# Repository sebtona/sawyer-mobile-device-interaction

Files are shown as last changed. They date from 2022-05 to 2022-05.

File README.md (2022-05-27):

# Sawyer Mobile Device Interaction
This was my final project in Advanced Robotics. I enabled the arm robot Sawyer to perform tapping, swiping, and pinching gestures on a stationary touch-enabled device. This is the first step toward having collaborative robots perform automated application/phone tests, or be teleoperated using human biological signals as inputs.

## Challenges
- Designing and manufacturing a new end effector for Sawyer-touch screen interaction
- Controlling force applied by Sawyer to touch screen
- Fixing mobile device in stationary, upright position

## Implementation
### Hardware
#### End Effector
- CAD models made in Autodesk Fusion 360 and new "fingers" 3D printed

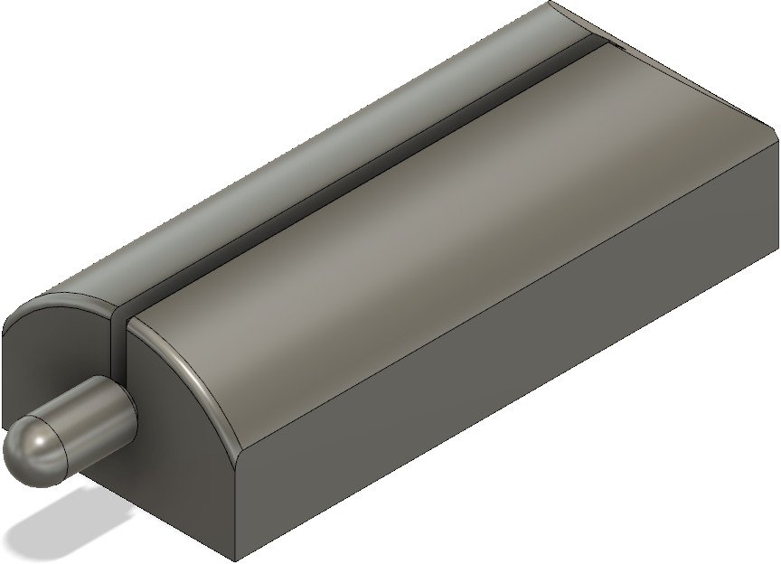
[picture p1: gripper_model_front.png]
CAD Model Front View
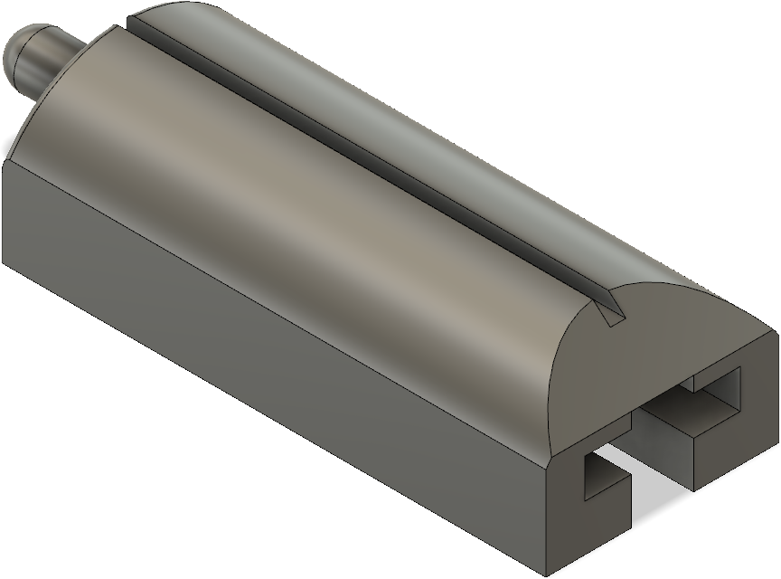
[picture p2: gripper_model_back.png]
CAD Model Back View
 
- Fingers slide and lock onto electric parallel gripper

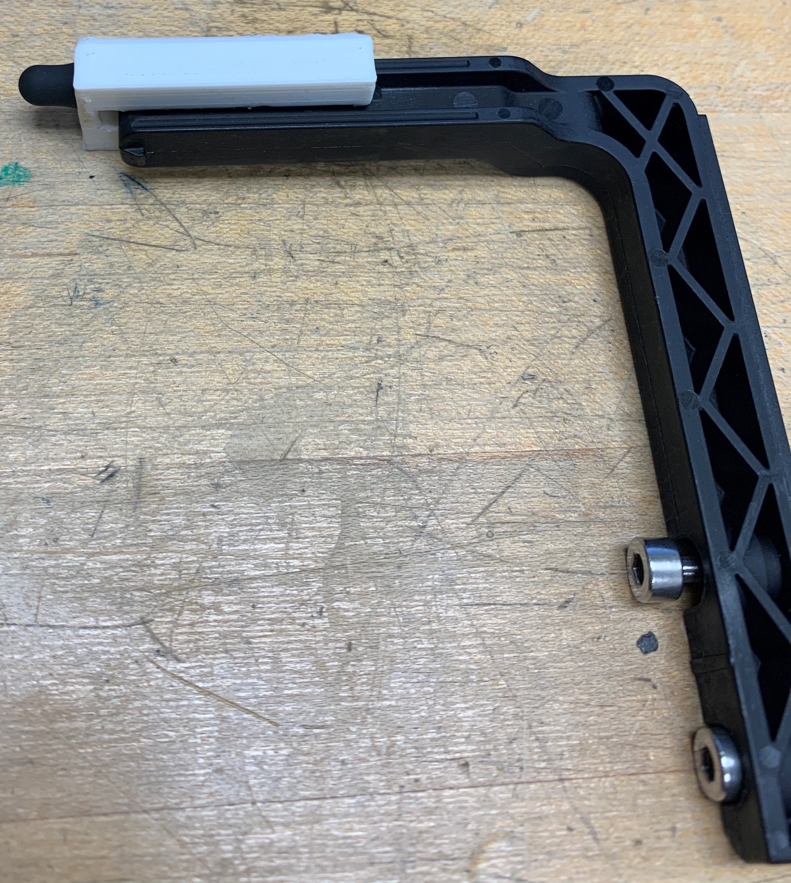
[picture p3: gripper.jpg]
Finger on gripper


- Capacitive stylus pen tips fixed to ends of fingers

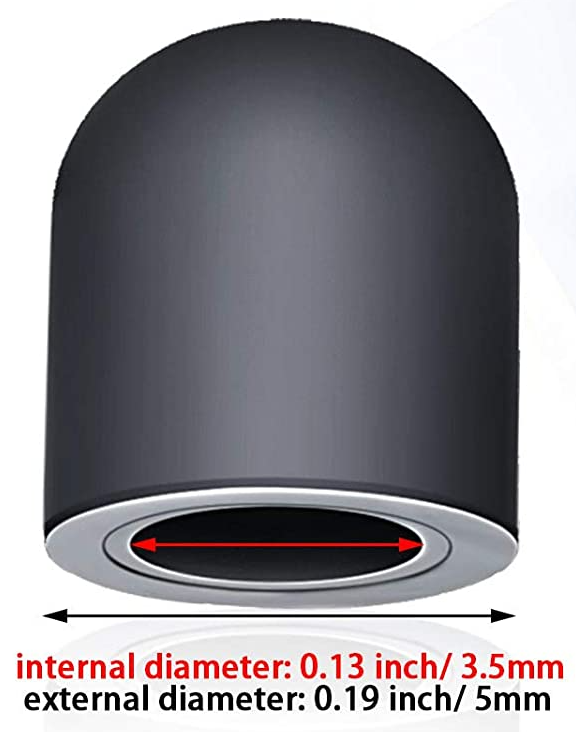
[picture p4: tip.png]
Stylus Pen Tip


- Grounding wires run from fingertips to Sawyer endpoint
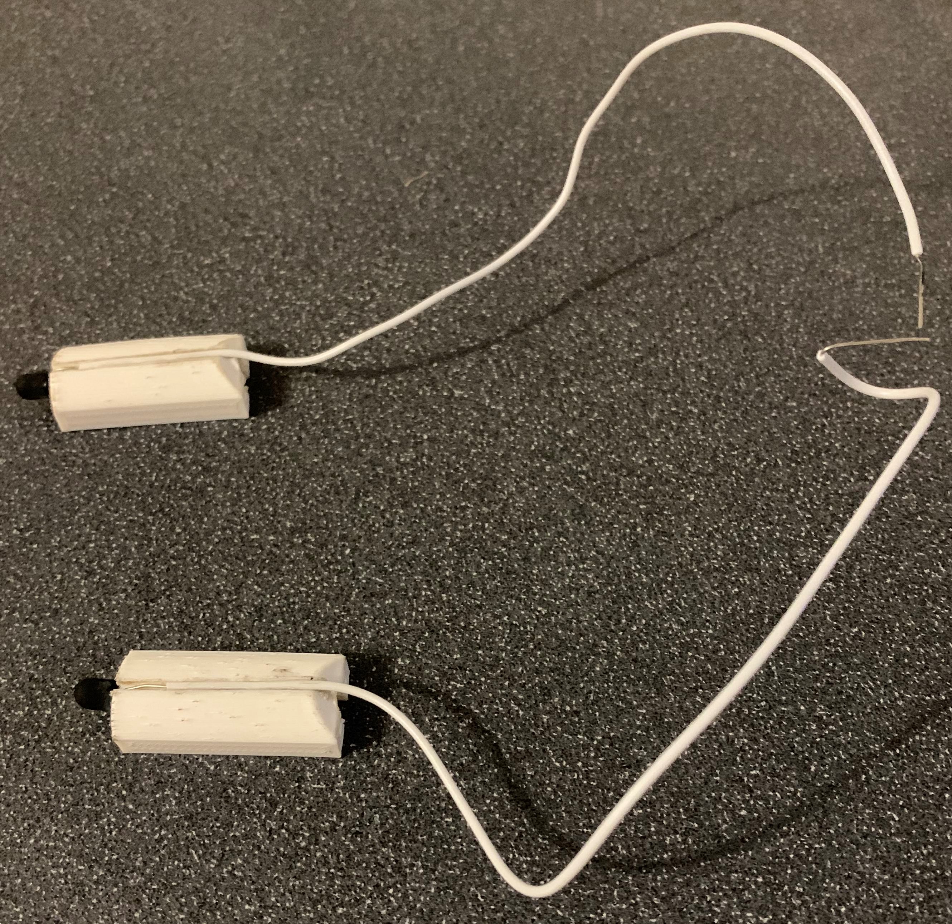
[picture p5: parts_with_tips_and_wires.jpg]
Finger Assembly


#### Mobile Device
- Fixed in one place using a metal pegboard and bolts

### Software
#### Sawyer
- Established LAN connection between Sawyer and workstation
- Booted Sawyer in Sawyer SDK mode to allow for communication through <a href="https://www.ros.org/" target="_blank">ROS</a>
- Created custom Python scripts for each gesture. Used <a href="https://rethinkrobotics.github.io/intera_sdk_docs/5.1.0/index.html" target="_blank">Intera SDK's</a> `intera_interface` library to access endpoint frame, joint angles, and force applied at endpoint
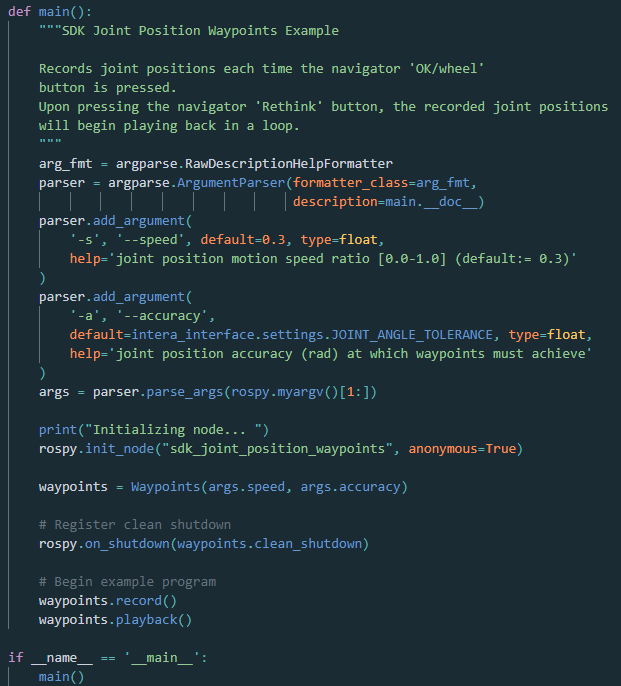
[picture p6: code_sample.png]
Code sample


- Explored alternative way to program Sawyer through built-in <a href="https://www.rethinkrobotics.com/intera" target="_blank">Intera</a> software platform
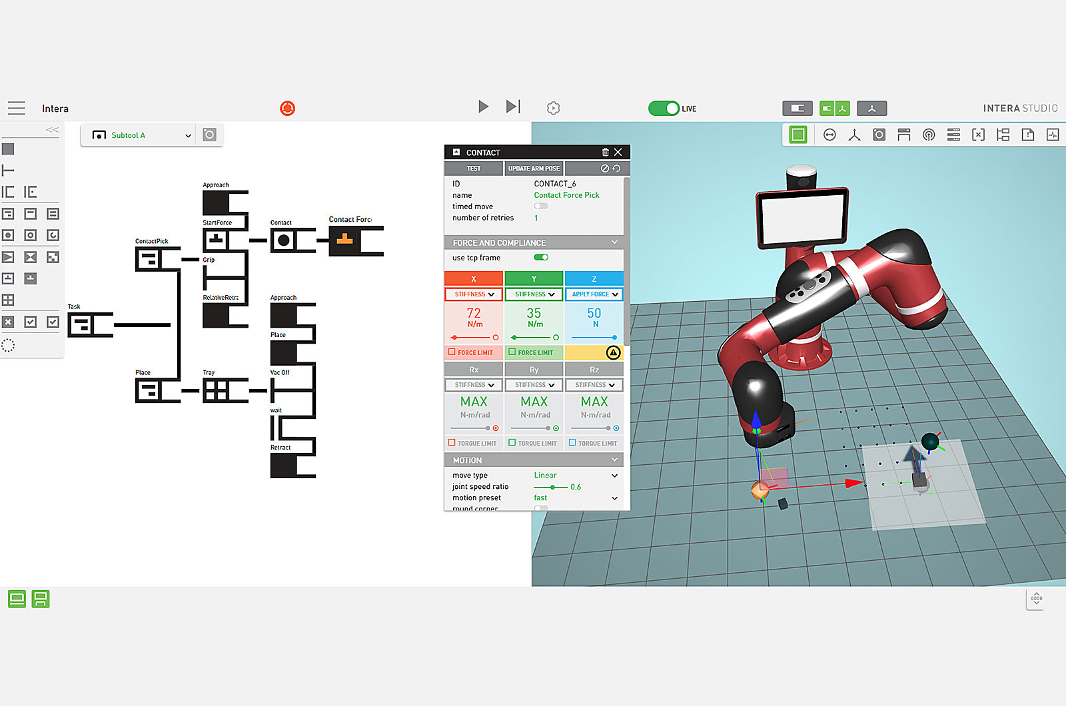
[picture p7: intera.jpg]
Intera Software


#### Mobile Device
- Used <a href="https://appadvice.com/app/touchscreen-test/1126113478" target="_blank">Touchscreen Test</a> mobile application as testing software to record each gesture being attempted on the device

## Deliverables
- Operation Demonstration

https://user-images.githubusercontent.com/46403390/170743748-325e1ee0-c41f-4d5c-8e6e-22a1d91676f6.mp4
- Project Presentation: https://github.com/sebtona/sawyer-mobile-device-interaction/blob/main/project_presentation.pptx
- IEEE Conference Paper: https://github.com/sebtona/sawyer-mobile-device-interaction/blob/main/ieee_conference_paper.pdf
- Python scripts: https://github.com/sebtona/sawyer-mobile-device-interaction/tree/main/scripts
- CAD model files
  - https://github.com/sebtona/sawyer-mobile-device-interaction/blob/main/touch_test_gripper.f3d
  - https://github.com/sebtona/sawyer-mobile-device-interaction/blob/main/touch_test_gripper.ipt
  - https://github.com/sebtona/sawyer-mobile-device-interaction/blob/main/touch_test_gripper.stl

## Environment Setup
### Sawyer
- Place Sawyer in front of a flat table within its workspace, ensure pegs or bolts can be secured into table and that the mobile device you are testing on can be held in place on the table by the pegs or bolts.
- Ensure that Sawyer's controller is connected to the same network as your development workstation using a CAT5 or CAT6 networking cable.
- Boot Sawyer normally, press the Rethink button to display the Head Screen Menu, use the Navigator Scroll Knob to select Info, then select About. Note Sawyer's IP address for later.
- Reboot Sawyer in SDK Mode by following the instructions in the "Switch Robot from Intera MFG to SDK Mode" section of <a href="https://support.rethinkrobotics.com/support/solutions/articles/80000980156-upgrade-sawyer-to-intera-sdk" target="_blank">this page</a>.
#### Gripper
- Acquire <a href="https://www.amazon.com/Zonon-Replacement-Conductive-Capacitive-Silicone/dp/B08P8MCZS1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" target="_blank">Conductive Stylus Tips</a>, Gorilla Glue, wire strippers/cutters, electrical tape, and about two feet of wire.
- 3D Print two tool tip parts using the included touch_test_gripper.stl file, or manufacture the parts based off of the included touch_test_gripper.f3d (Fusion 360) file.
- Cut the wire in half, and strip both ends of both pieces. Wrap the end of one wire around the base of the base of the stylus tip section for each tool tip part, and lay the rest of each wire in each tool tip part's groove. Carefully Gorilla Glue the capacitive stylus tips onto the ends of each tool tip part, ensuring that they make permanent contact with the exposed wire. Gorilla Glue the unexposed wire sections into the tool tip part grooves. Slide each assembly onto Sawyer's electric parallel gripper, and use electrical tape to secure the ends of each wire to a conductive part of Sawyer's end effector.

### Workstation
- Follow the instructions <a href="https://sdk.rethinkrobotics.com/intera/Workstation_Setup" target="_blank">here</a> for initial setup of your development workstation. Enter Sawyer's IP address (noted earlier) in the 'robot_hostname' field of the intera.sh file. You do not need to setup Rviz.
- In a new terminal, navigate to your source folder and create a new package:
```sh
cd ~/ros_ws/src
catkin_create_pkg touch_test std_msgs rospy roscpp
cd ..
catkin_make
```
- Copy the included scripts folder and its contents into your new touch_test package directory.
- Ensure that all Python scripts are executable, then run another catkin_make:
```sh
cd ~/ros_ws/src/touch_test/scripts
sudo chmod +x get_endpoint_forces.py get_endpoint_pose.py get_joint_angles.py pinch.py swipe_left.py swipe_right.py tap.py
cd ~/ros_ws
catkin_make
```
- Reinitialize your SDK environment and reverify your connection to Sawyer's controller:
```sh
cd ~/ros_ws
./intera.sh
env | grep ROS
rostopic list
```

## Running Code
- Make sure you are in the SDK environment, you have sourced your workspace, and that you are in your root workspace folder:
```sh
cd ~/ros_ws
./intera.sh
source devel/setup.bash
```
- Rosrun any Python script you choose with the following syntax:
```sh
rosrun [package] [Python file]
```
- Example:
```sh
rosrun touch_test pinch.py
```

## Future Work
- ISR when applied force reaches set threshold
- Repeatability testing
- Add computer vision to recognize text/buttons and their relative positions
- Teleoperation using biological signals like EMG or gaze

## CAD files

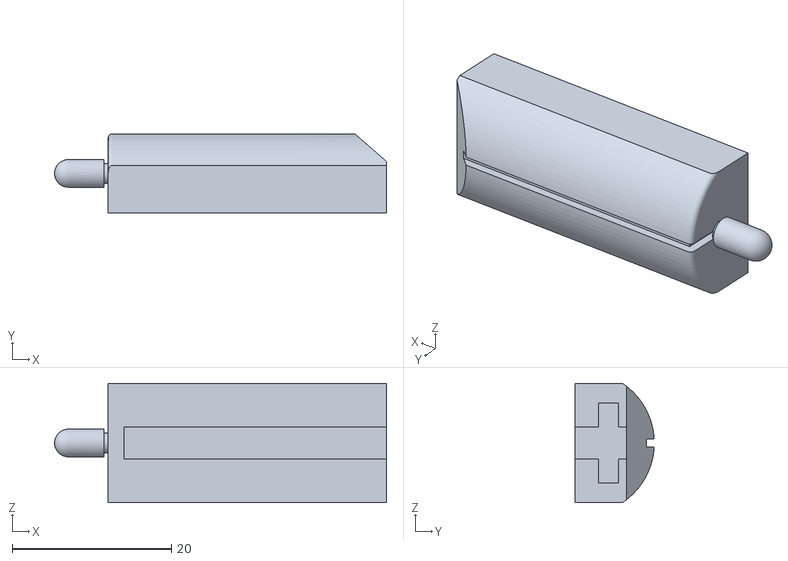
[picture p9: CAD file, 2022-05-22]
touch_test_gripper.stl
41.8 x 9.99 x 15.0

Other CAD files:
touch_test_gripper.f3d
touch_test_gripper.ipt
